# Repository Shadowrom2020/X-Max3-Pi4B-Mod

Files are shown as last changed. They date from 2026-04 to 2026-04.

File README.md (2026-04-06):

# X-Max3-Pi4B-Mod
A simple mod for the Qidi X-Max 3 to run on a Rasperry Pi 4B instead of the weak RK3328 SoC

# DISCLAIMER :warning:

**WARNING:** This modification requires knowledge of electronics and embedded systems. Do not attempt this procedure if you are not confident in your technical abilities.

**NO WARRANTY.** The information, instructions, files, and materials in this repository are provided "as is" and without warranty of any kind, either express or implied, including but not limited to the implied warranties of merchantability, fitness for a particular purpose, and non-infringement.

**LIMITATION OF LIABILITY.** To the fullest extent permitted by applicable law, the author shall not be liable for any direct, indirect, incidental, special, exemplary, or consequential damages whatsoever (including, but not limited to, damage to or destruction of hardware, loss of data, loss of revenue, or business interruption) arising out of or in connection with the use of, or inability to use, the information or materials in this repository, even if the author has been advised of the possibility of such damages.

**ASSUMPTION OF RISK.** By proceeding with this modification, you acknowledge that you have read and understood this disclaimer, that you are undertaking the modification entirely at your own risk, and that you assume sole responsibility for any and all consequences, including hardware damage, that may result.

## Prerequisites
You need:
- A X-Max 3 Printer with a X-6 V1.0 Motherboard
- A Raspberry Pi 4B with a micro SD card for the OS (>=32GB)
- 2 USB-A to USB-C cables of approximately 30-50cm length one angled by 90°
- A Step down power converter 24V -> 5V 3A [like this for example](https://www.berrybase.de/netzteilmodul-6-40v-5v-3a-mit-2x-usb-ausgang)
- 1 female USB C breakout board
- 1 male USB A breakout board
- 1 male USB C breakout board
- Some cables (0.5mm² e.g.: red, black, white, blue)
- 2 cable shoes (ring or the open variant)
- 4 Breadboard connection cables (as short as possible) female to male for the serial port connection to the stock screen
- A second micro SD Card (8-32GB) to flash the mainboard

## Preparations

### Printed parts
- Print the Pi4 Holder in the STL folder and mount your Raspberry Pi4 to it. Or design your own...

### Cables and electronics

You need a Y-Cable for the toolhead connection. Because the toolhead operates with 24V, this would turn your Raspberry Pi into a beautiful smoke machine.
So grab the USB breakout boards and build one:
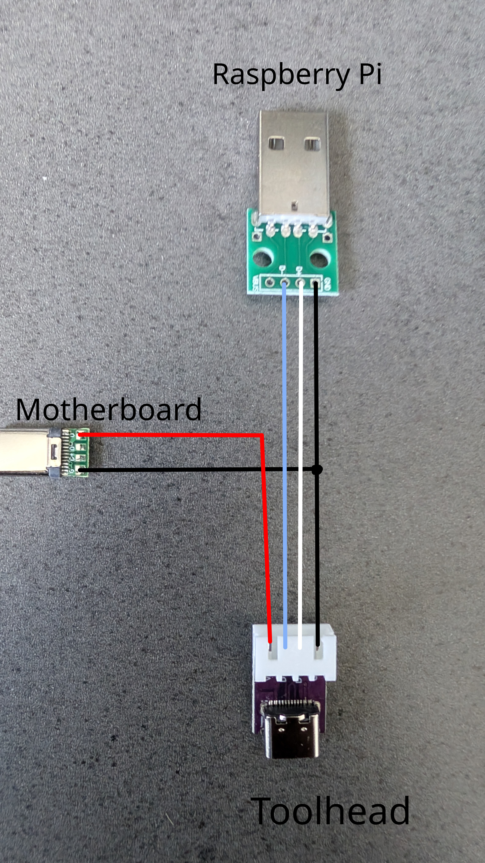
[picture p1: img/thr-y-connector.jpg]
THR-Y-Connector image


### Installation

- Install Rasbian on your Pi, use a version without GUI
- Backup your system
- Shut down and remove the power connector
- Open the back plate
- Remove the EMMC from the mainboard and store it in a safe location
- Remove the USB and Ethernet cables from the Motherboard
- Remove the USB C cable for the toolhead (Number 2 in the image below)
- Unplug the serial cable for the screen (Number 5 in the image below)
- Mount the Pi to the screw point
- Wire up the PI, plug Ethernet and USB Cables into the Pi
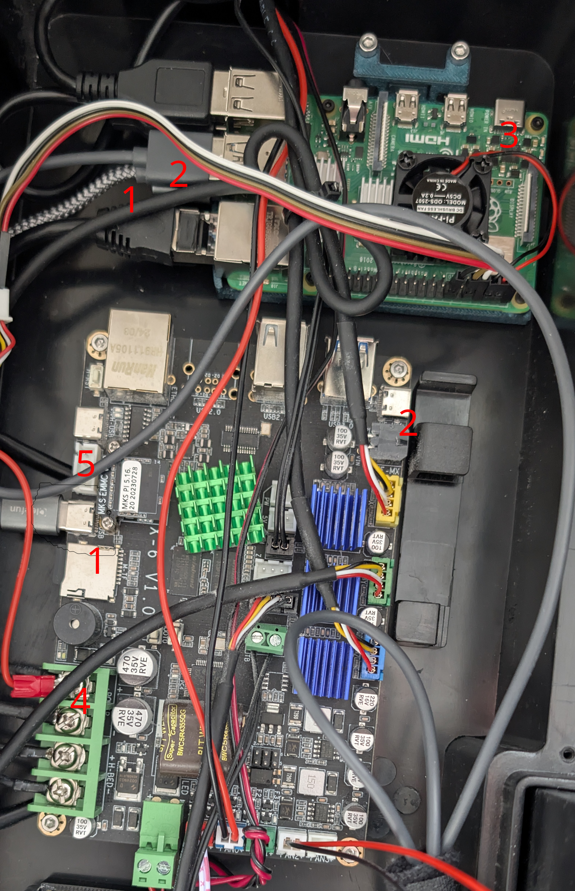
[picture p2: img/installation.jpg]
Installation image

- Connect the Pi to the Mainboard MCU via USB A to USB C cable (Number 1 in the above image)
- Connect the Y-Cable to your PI and your Mainboard (Number 2 in image) connect the USB C cable from the toolhead to the Y-Connector
- Connect your Step down power converter to the 24V input on the motherboard (4). Use appropriate cable shoes for this.
- Plug a USB-Cable into the step down converter and connect it to the Pi (3). You'll need a short USB connector or one that is angled by 90° because of limited space
- Connect the breadboard connectors to the serial port of the Raspberry Pi see [this tutorial](https://randomnerdtutorials.com/raspberry-pi-pinout-gpios/) Pin 4 (VCC), Pin 6 (GND), Pin 8 (TX) and Pin 10 (RX)
- Connect the male side of the breadboard connectors to the serial port cable for the screen. Connect the pins 1 on 1 (VCC to VCC, GND to GND, RX to RX, TX to TX)
UART pinout

### Software
- Boot up the system
- Enable the serial port using raspi-config (Terminal no, activate yes)
- Install Klipper, Moonraker, Mainsail, Crowsnest and other software 
- Build klipper firmware for the Mainboard MCU with these settings:
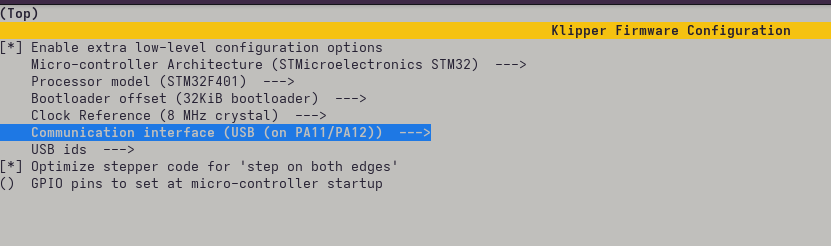
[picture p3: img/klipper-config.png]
klipper menucoinfig

- Copy the klipper.bin to your second micro SD and rename it to X_4.bin
- Shut down the printer
- Insert the SD card to the SD Slot on the X-6 mainboard
- Start the printer
- Now you should see two devices in /dev/serial/by-id/ one is the THR the other is the Motherboard
devices
- Install FreeDi to make the screen works [FreeDi](https://github.com/Phil1988/FreeDi).
  Clone the repository and run: FreeDi/install.sh
  When prompted if you're using the stock mainboard, chose no!
- Edit the FreeDi.cfg and set the Serial Port to /dev/ttyS0
- Reboot the system and complete the FreeDi wizard, this will add a base config for the printer
- Edit printer.cfg and change the serial port of the MCU to the new serial port
- Crowsnest won't work after FreeDi setup, you'll have to reconfigure it

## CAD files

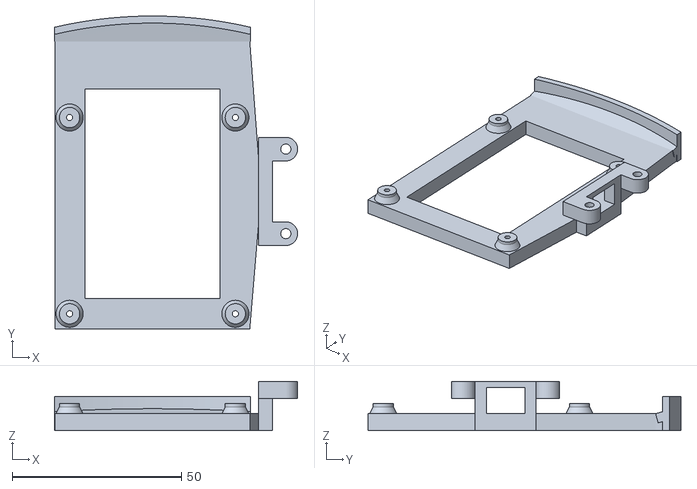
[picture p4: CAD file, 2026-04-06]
STL/Pi4.stl
71.9 x 92.5 x 14.5
